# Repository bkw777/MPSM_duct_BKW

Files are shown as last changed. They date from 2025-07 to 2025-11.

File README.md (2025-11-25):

# MPSM_Duct

Hotend fan and part cooling blower duct for Monoprice Select Mini 3d printer.

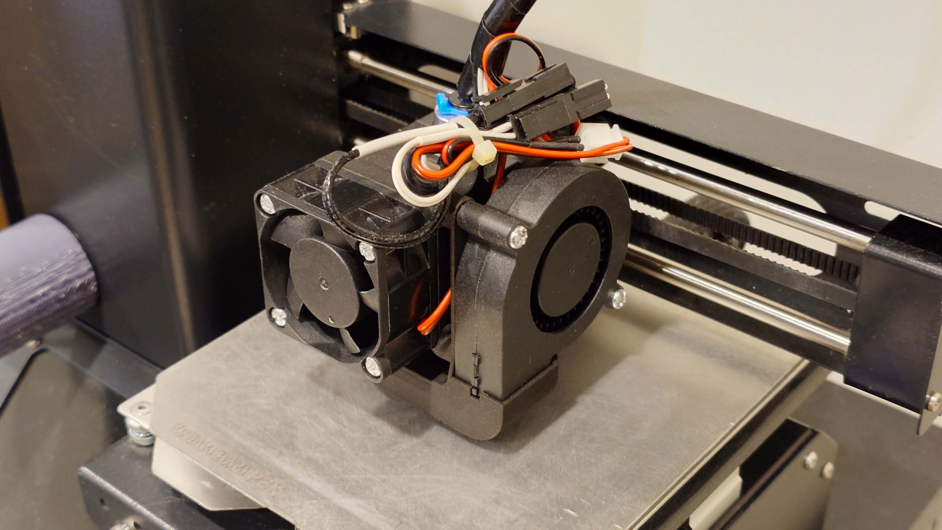
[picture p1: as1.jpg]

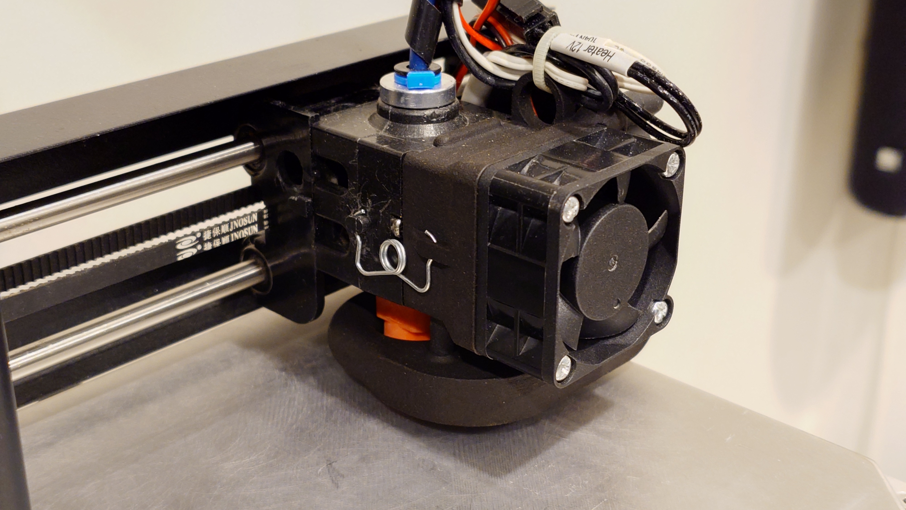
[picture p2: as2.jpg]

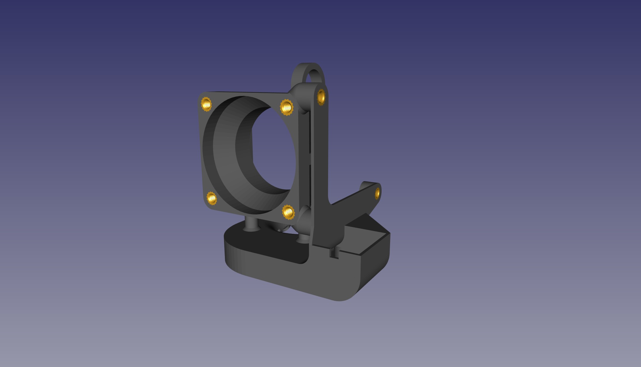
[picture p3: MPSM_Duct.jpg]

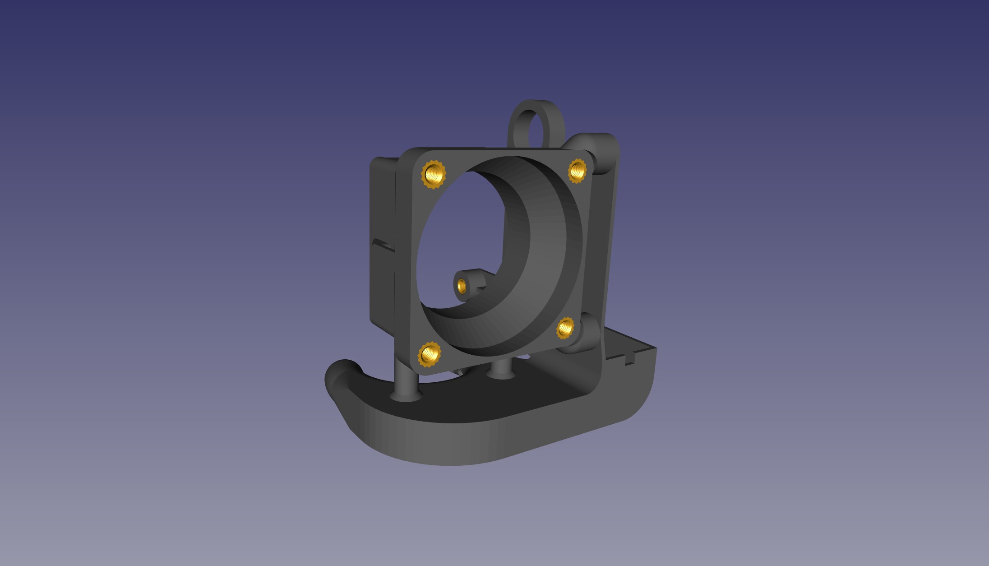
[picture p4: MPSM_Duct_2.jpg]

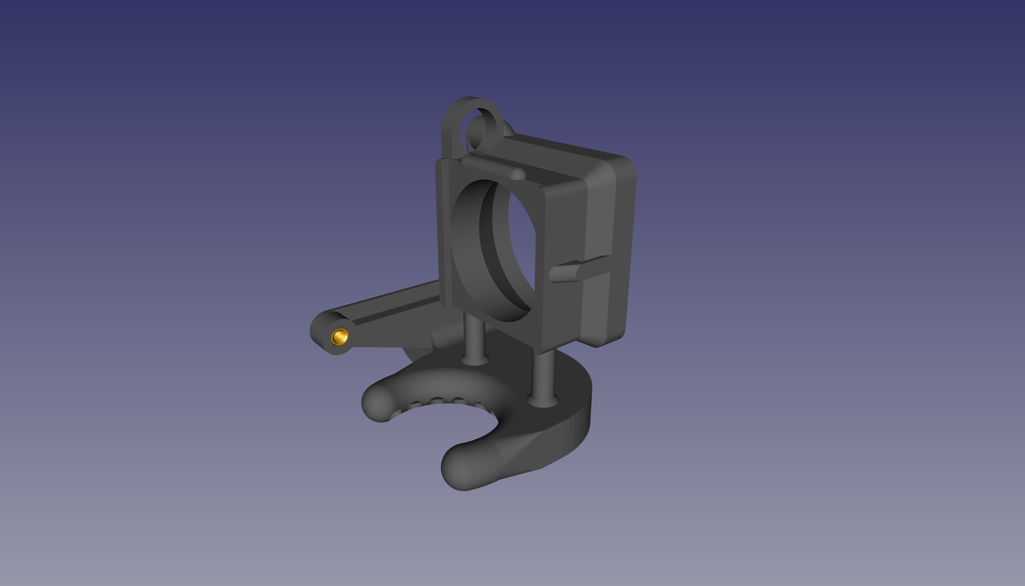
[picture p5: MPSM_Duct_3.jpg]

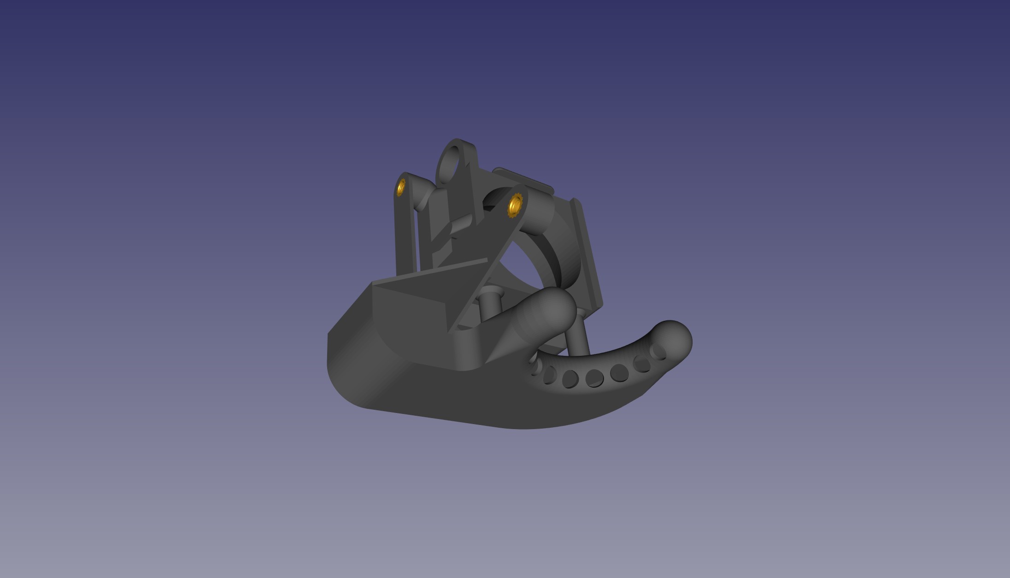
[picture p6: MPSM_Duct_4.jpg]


The model is highly parametric and uses the customizer panel in OpenSCAD to adjust all kinds of things.  

The major options are:  
* Fan size: 40mm, 35mm, 30mm
* Screw holes sized for screwing directly into the plastic, or pockets for heat-set inserts

Other options:
* Stock vs [CHC](https://trianglelab.net/products/chcceramic-heating-core-kit?VariantsId=10256) heater cartridge
* Degrees of wrap around the nozzle.

40mm fan  
You don't need a 40x20 like this. A silent Noctua 40x10 would be plenty considering the original fan is only 30x10 and did both the heat-break and the part cooling.  
By itself a larger fan like this doesn't do as much good as it could, because the stock carriage doesn't provide very much air flow behind the heat-sink. It's intentionally slightly restrictive to force some of the air to go down to the stock part cooling duct. It's possible to drill 4 more holes in the carriage between the heat-sink and the rails without even taking the printer apart. 8mm or 5/16" drill, one vertical in the center right in front of the rails, through the top & bottom, and one horizontal between the rails. Adds 4 more 8-9mm holes for hot-end fan air to exhaust.  
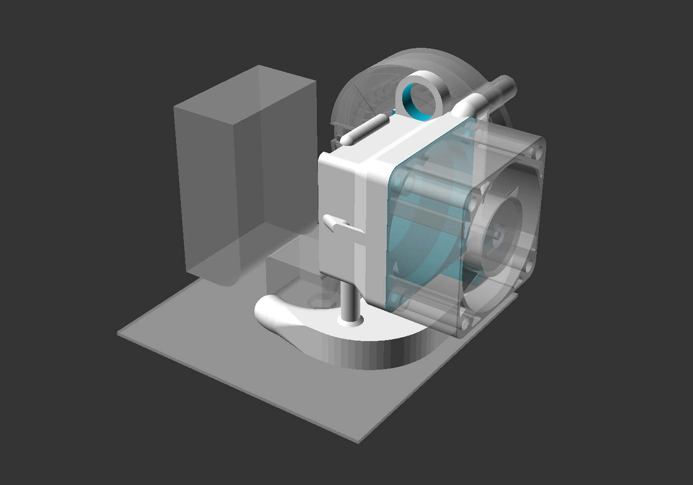
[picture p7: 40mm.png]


35mm fan  
35mm is a less common size but they do exist and the hot-end duct on the printer happens to be 35mm so it looks visually neat.  
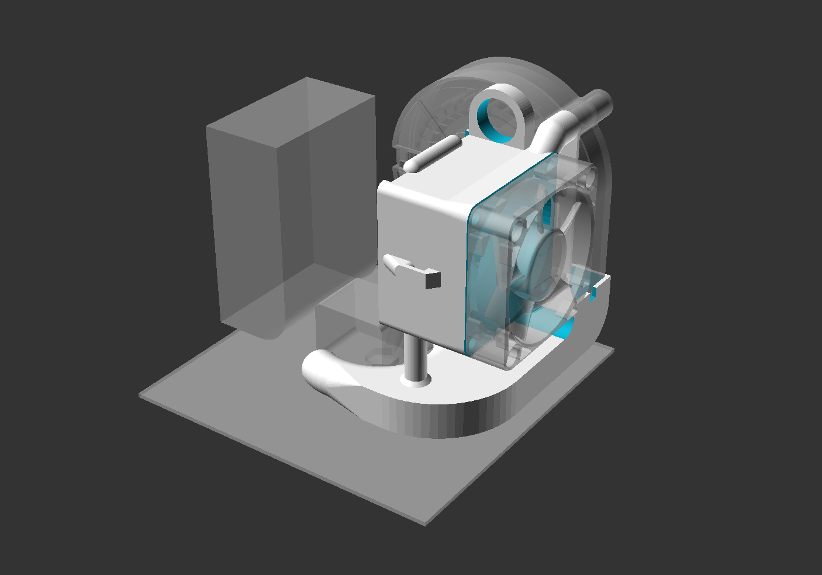
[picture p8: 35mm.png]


30mm fan  
This doesn't look the best, but the usefulness is the original fan is 30mm, so with this version you can re-use the original fan.  
It's still an improvement over stock because now it's dedicated 100% to the heat-break, and remember a standard E3D V6 only has a 30mm fan, so this should actually be fine.  
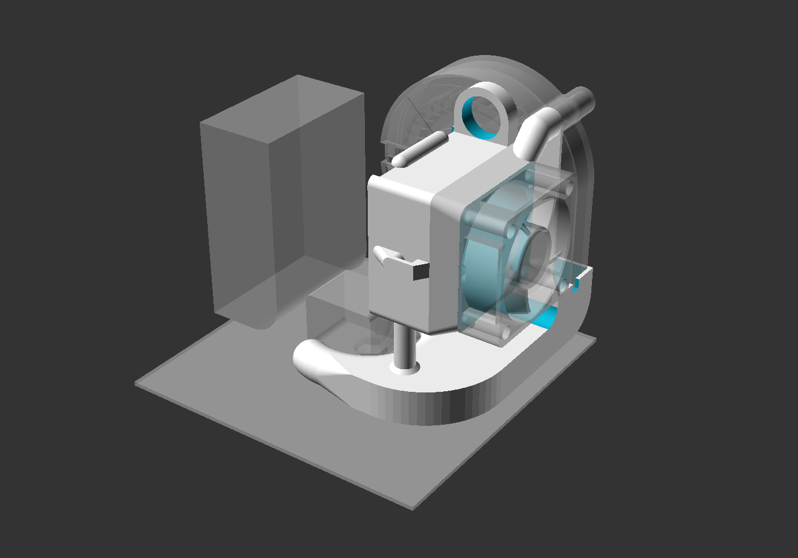
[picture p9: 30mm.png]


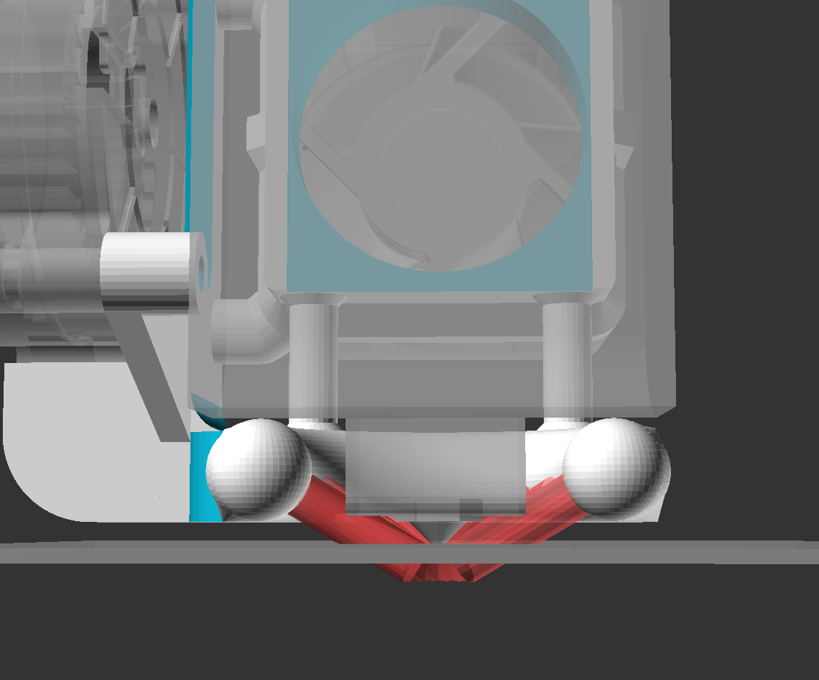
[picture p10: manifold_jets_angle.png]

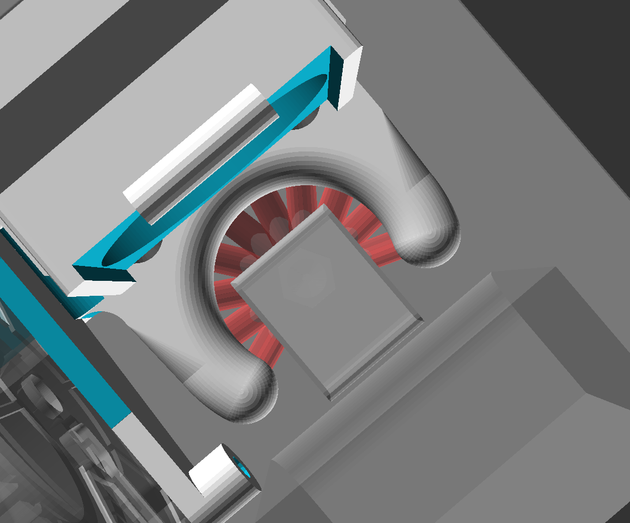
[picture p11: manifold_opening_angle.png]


With a CHC heater, the blower output manifold can go all the way around the nozzle in a donut, and the duct & manifold tube can be a little bigger.

Stock heat block:  
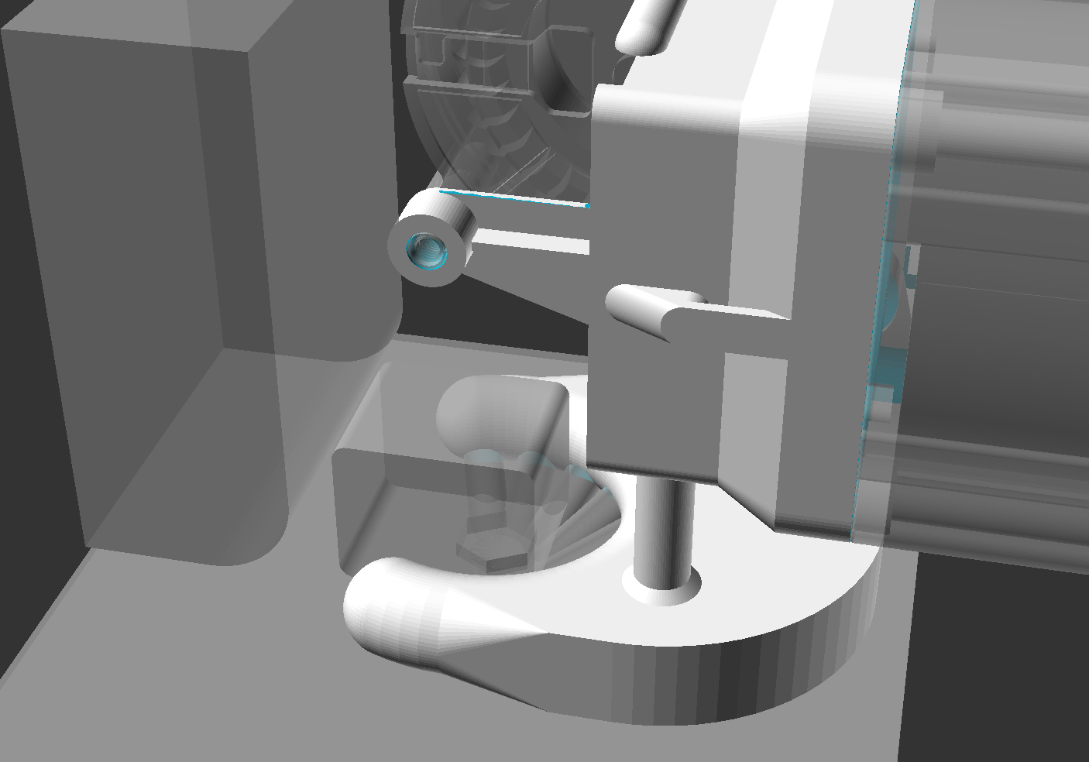
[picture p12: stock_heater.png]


CHC ceramic heater cartridge:  
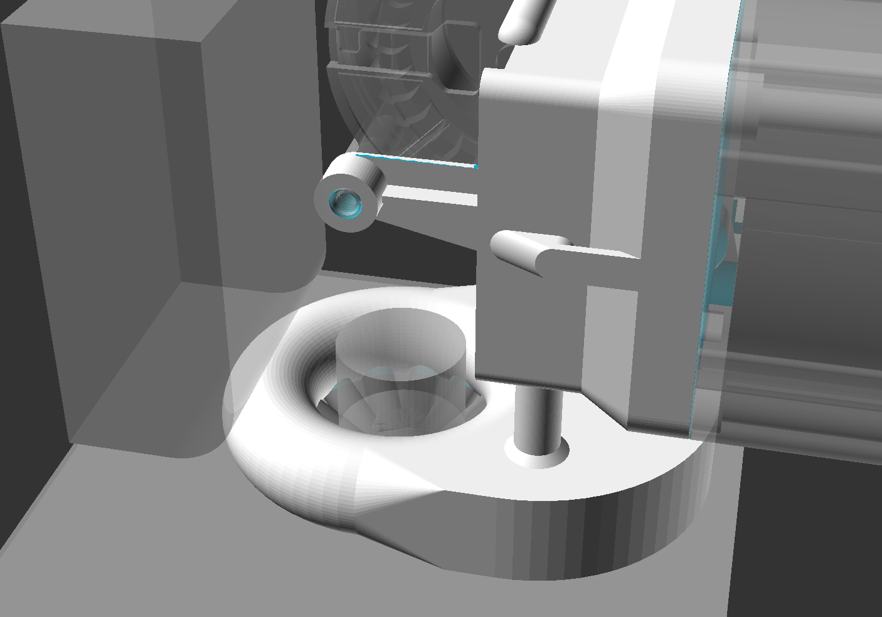
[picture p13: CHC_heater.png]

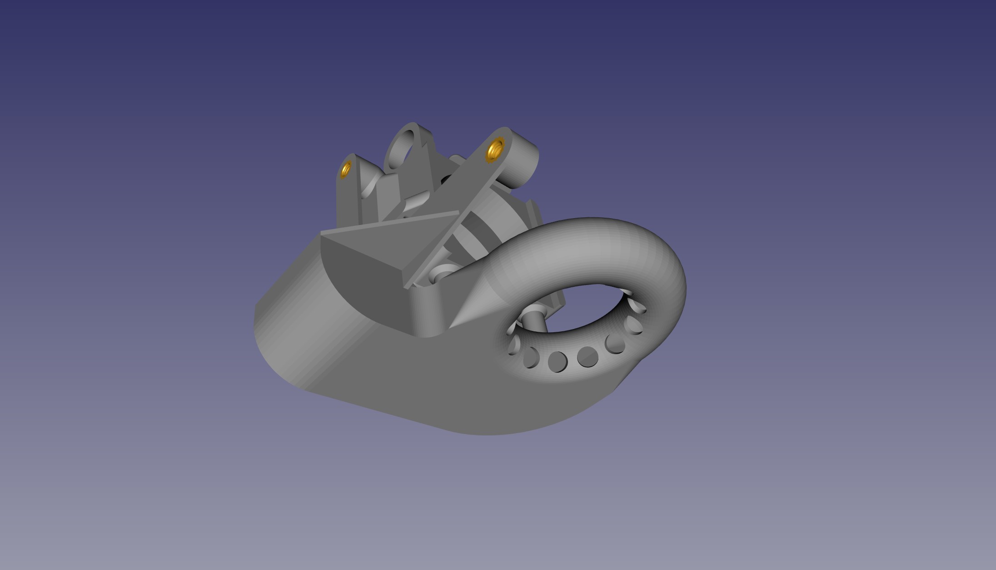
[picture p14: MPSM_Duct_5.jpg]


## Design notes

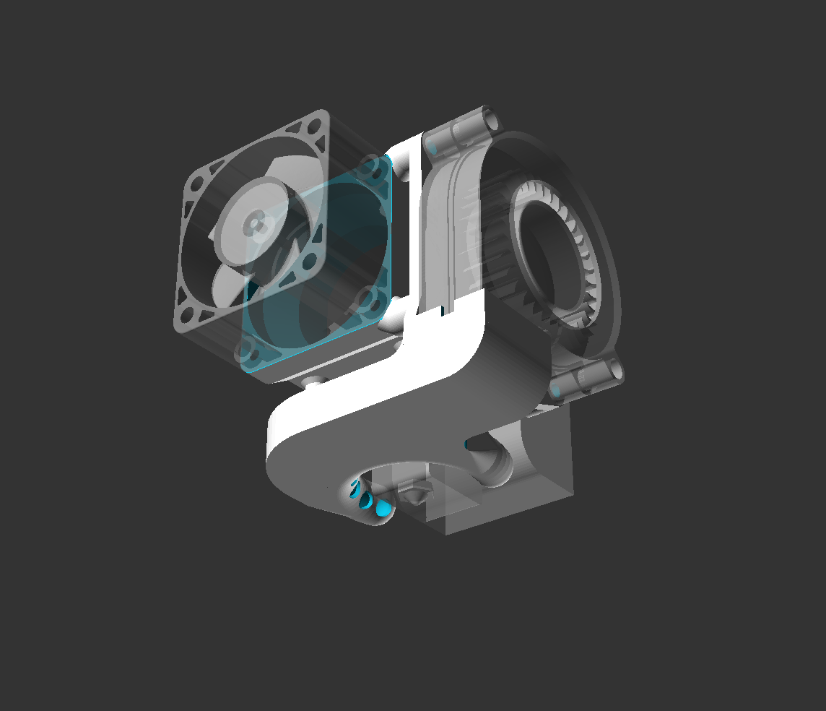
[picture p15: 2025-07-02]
MPSM_Duct_2.png

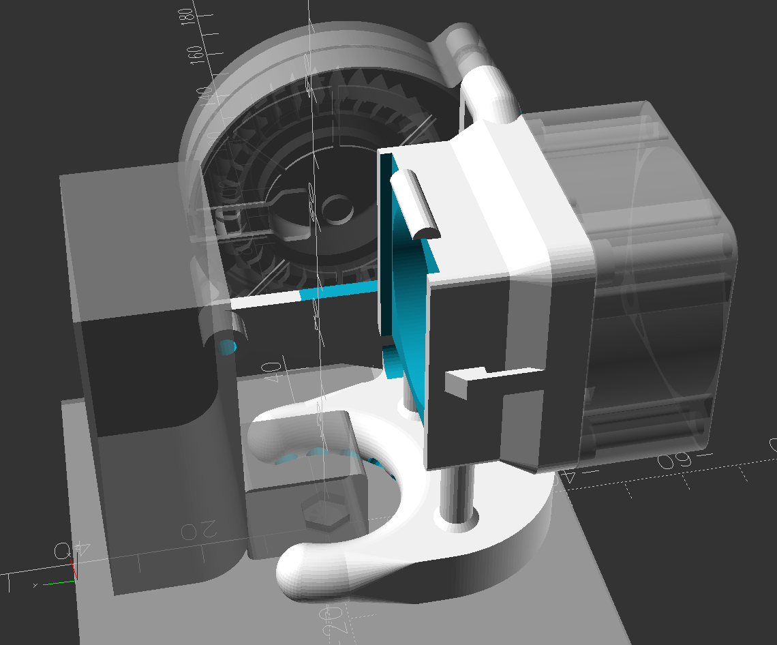
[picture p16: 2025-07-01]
MPSM_Duct_1.png

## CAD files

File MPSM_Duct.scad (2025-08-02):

// Hotend fan and part cooling duct for Monoprice Select Mini V2 E3D
// CC-BY-SA 2025 Brian K. White
//
// Use the Customizer window to select options.
// <design default> = 40mm fan, no screw inserts, stock heat block

hotend_fan_size = 40; // [30,35,40]
hf_w = hotend_fan_size;
screw_hole_inserts = false;
heater_type = "stock"; // ["stock","v6","chc"]


/* [Site Objects] */
show_fans = true;
show_inserts = true;
show_nozzle = true;
show_build_plate = true;
show_carriage = true;
show_jets = true;

/* [Debug Cutaways] */
cutaway_top = false;
cutaway_top_z = 0;
cutaway_bottom = false;
cutaway_bottom_z = 11;
cutaway_left = false;
cutaway_left_x = 0;
cutaway_right = false;
cutaway_right_x = 0;
cutaway_front = false;
cutaway_front_y = -4;
cutaway_back = false;
cutaway_back_y = -4;

/* [Hidden] */
// screw sizes, screw hole id, heatsert hole id, hole depth
// SIZE[ID_bare,ID_heatsert,depth]
M2_5 = [2,3.7,5];
M3 = [2.8,4.3,6];
M4 = [3.6,5.6,8.5];

/* [Misc] */
wire_anchor = true;
clearance_above_print = 2;
fitment_clearance = 0.2;
fc = fitment_clearance;
wall_thickness = 1; // .1
wt = wall_thickness;
small_corner_radius = 2; // .1

top_ledge_style = 2; // [0:"None",1,2,3]

/* [Spring Hooks] */
spring_hook_inset = 6;
hz = spring_hook_inset;
spring_hook_clearance = 3;

/* [Manifold] */
manifold_jets_angle = 35;
manifold_opening_angle = 140;
manifold_jets_diameter = 4; // .1
manifold_jets = 10;

/* [Hotend Fan] */
// hotend fan bolt pattern
hf_bp = 
  (hf_w==30) ? 24 :
  (hf_w==35) ? 29 :
  (hf_w==40) ? 32 :
  (hf_w==50) ? 40 :
  0 ;
//echo("hotend fan size (hf_w)",hf_w);
//echo("hotend fan bolt pattern (hf_bp)",hf_bp);


shd = screw_hole_inserts?1:0;

// -1 = auto
hotend_fan_screw_hole_diameter = -1; // .1
hf_sid =
  (hotend_fan_screw_hole_diameter>=0) ? hotend_fan_screw_hole_diameter :
  (hf_w==30) ? M2_5[shd] :
  (hf_w<=40) ? M3[shd] :
  M4[shd] ;
//echo("hotend fan screw hole id (hf_sid)",hf_sid);

// -1 = auto
hotend_fan_screw_hole_depth = -1; // .1
hf_sih =
  (hotend_fan_screw_hole_depth>=0) ? hotend_fan_screw_hole_depth :
  (hf_w<50) ? 6 : 8 ;
//echo("hotend fan screw hole depth (hf_sih)",hf_sih);

// -1 = auto
hotend_fan_corner_radius = -1; // .1
hf_cr = (hotend_fan_corner_radius<0)?(hf_w-hf_bp)/2:hotend_fan_corner_radius;

hotend_fan_flange_elevation = 14;
hf_fz = hotend_fan_flange_elevation;

// -1 = auto
hotend_fan_flange_thickness = -1;
hf_ft = (hotend_fan_flange_thickness<0)?hf_sih:hotend_fan_flange_thickness;
hf_z = hf_fz + hf_ft;

// hotend fan ID
hf_id = hf_w-wt*2;

hotend_width = 35; // [34:"34 (square, and more room for spring clip)",35:"35 (flush with mating part)"]

/* [Hidden] */
hotend_fan_thickness = 20;
hf_t = hotend_fan_thickness;

// dimensions of various parts, not customizable options

// hotend cover interface
hew = hotend_width;  // hotend width
heh = 34;  // hotend height
// "hotend block" is the step on the hotend cover interface
hebw = 30; // hotend block width
hebt = 2;  // hotend block thickness

// hotend face (z=0) to center of nozzle
nozzle_y = -14;

// center of hotend fan to nozzle tip
nozzle_z = -42;

bottom_y = nozzle_z+clearance_above_print;

total_h = hebt + hf_z;

// part blower
// facing inlet, outlet down
// relative to motor axle
pb_tlx = -23;  // top left screw
pb_tly = 20;   // top left screw
pb_brx = 20;   // bottom right screw
pb_bry = -18;  // bottom right screw
pb_le = -27.5; // left edge
pb_be = -25.5; // bottom edge
pb_ow = 20.1;  // outlet width
pb_od = 15.1;  // outlet depth
pb_oh = 2.5;   // outlet height

/* [Part Blower] */

// -1 = auto
part_blower_screw_hole_diameter = -1; // .1
pb_sid =
  (part_blower_screw_hole_diameter>=0) ? part_blower_screw_hole_diameter :
  M3[shd];
// -1 = auto
part_blower_screw_hole_depth = -1; // .1
pb_sih =
  (part_blower_screw_hole_depth>=0) ? part_blower_screw_hole_depth:
  M3[2];
//echo ("part blower screw hole id,depth (pb_sid,pb_sih)",pb_sid,pb_sih);

part_blower_mount_plate_thickness = 1;
part_blower_lower_post = true;
part_blower_lower_brace_depth = 3;

part_blower_x = 0;
pb_x = part_blower_x + (hf_w>=40 ? hf_w/2+pb_sih : 20+pb_sih);

part_blower_y = -1;
pb_y = part_blower_y;

part_blower_z = 6;
pb_z = part_blower_z;


// manifold width vs height
//
// The Z tower comes to within 21mm from the nozzle,
// so we set a hard limit of 42mm wide for anything
// symmetrical centered on the nozzle.
//
// The size of the manifold tubes is whatever can fit between
// the 42mm max width and the heat block.
/* [Hidden] */
max_manifold_width = 42;

/* [Manifold] */
heater_clearance_radius = 12;
pd_nr = heater_clearance_radius;

// 0 = max
part_cooler_manifold_width = 0;
pd_mw = (part_cooler_manifold_width ? part_cooler_manifold_width : max_manifold_width );
assert(pd_mw<=max_manifold_width,"Manifold width > 42mm hits the Z tower!");
// 0 = auto
part_cooler_manifold_height = 0;
pd_mh = (part_cooler_manifold_height ? part_cooler_manifold_height : pd_mw/2-pd_nr );


// TODO shift 50mm fan off center to avoid hitting Z tower

/* [Part Duct] */
part_cooler_duct_fillet_radius = 4;
pd_fr = part_cooler_duct_fillet_radius;
pillar_diameter = 5;
pillar_chamfer = 1; // .1
pillar_y = -4;

/* [Hidden] */
e = 0.01;
//$fa = 1;
//$fs = $preview?0.6:0.4;
$fn = 72;

module fan () {
  stl =
    hf_w==30 ? "lib/fan3010.stl" :
    hf_w==35 ? "lib/fan3510.stl" :
    hf_w==40 ? "lib/fan4020.stl" :
    "";
  if (stl) import(stl);
}

module blower () {
  import("lib/blower5015.stl");
}

module heatsert (d) {
  echo ("heatsert(d)",d);
  if ( (d>M2_5[1]-0.5) && (d<M2_5[1]+0.5) ) rotate([180,0,0]) import("lib/insert_m2_5.stl");
  else if ( (d>M3[1]-0.5) && (d<M3[1]+0.5) ) rotate([180,0,0]) import("lib/insert_m3.stl");
  else if ( (d>M4[1]-0.5) && (d<M4[1]+0.5) ) rotate([180,0,0]) import("lib/insert_m4.stl");
}

module mirror_copy(v = [1, 0, 0]) {
  children();
  if (v[0]||v[1]||v[2]) mirror(v) children();
}

module qc (w=10,d=10,h=10,r=1) {
  mirror_copy([0,1,0]) translate([0,d/2,0])
    mirror_copy([1,0,0]) translate([w/2,0,0])
      cylinder(h=h,r=(r<e?e:r));
}

module sqylinder(w=10,d=10,h=10,r=1) {
  if (r<=0) translate([-w/2,-d/2,0]) cube([w,d,h]);
  else hull() qc(w=w-r*2,d=d-r*2,h=h,r=r);
}

module fan_flange (w,s,h,r,d,t=wt) {
  ch = h+2*e;
  id = w-2*t;
  difference() {
    sqylinder(w=w,d=w,h=h,r=r);
    translate([0,0,-e]) {
      qc(w=s,d=s,h=ch,r=d/2);
      cylinder(d=id,h=ch);
    }
  }
}

module taurus(R=10,r=4,A=360,a=0){
  rotate_extrude(angle=A,start=a) translate([R-r,0,0]) circle(r=r);
}

module nozzle () {
  //nozzle
  pd = 1.25; // point diameter
  ph = 2;    // point height
  hh = (heater_type=="stock"?2:3);    // hex height
  cylinder(d1=pd,d2=pd+2*ph,h=ph);
  translate([0,0,ph]) cylinder(d=8.1,h=hh,$fn=6);

  // heat block
  if (heater_type=="v6") {
    w = 16;
    d = 23;
    h = 12;
    s = 1.5; // sock thickness
    i = 8; // inset, nozzle to edge
    translate([0,d/2-8,h/2+ph+hh])
      cube([w+2*s,d+2*s,h+2*s],center=true);
  } else if (heater_type=="chc") {
    translate([0,0,ph+hh])
      cylinder(d=15,h=12);
  } else {
    // stock
    w = 15;
    d = 16;
    h = 12;
    b = 1.5; // blanket thickness
    i = 4; // inset (nozzle to edge)
    translate([w/2,d/2-i,h/2+ph+hh])
      rotate([-90,0,90])
        sqylinder(w=d+2*b,d=h+2*b,h=w,r=b);
  }

}

module carriage () {
  w = 35;
  d = 20;
  h = 50;
  y = 14; // nozzle to front of carriage
  z = 10; // nozzle to bottom of carriage
  r = 8;
  hull() {
    translate([-w/2,y+d-e,z]) cube([w,e,e]);
    translate([-w/2,y+d-e,z+h-e]) cube([w,e,e]);
    translate([-w/2,y,z+h-e]) cube([w,e,e]);
    translate([-w/2,r+y,r+z]) rotate([0,90,0]) cylinder(r=r,h=w);
  }
}


//////////////////////////////////////////////////////////////////////////////////

module anchor() {
  w = hf_fz;
  d = w/2;
  h = 4;
  difference() {
    group() {
      translate([0,d,0]) cylinder(d=w,h=h);
      translate([-w/2,0,0]) cube([w,d,h]);
    }
    translate([0,d,-e]) cylinder(d=w-4,h=h+2*e);
  }
}

module hotend_fan_duct() {
  if(show_fans) translate([0,0,hf_z]) %fan();
  if(screw_hole_inserts && show_inserts)
    mirror_copy([0,1,0]) mirror_copy([1,0,0]) translate([hf_bp/2,hf_bp/2,hf_z]) %heatsert(hf_sid);
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

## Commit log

2025-06-30 polish blower mount
    [MPSM_duct_BKW.scad]
2025-07-01 fillets on duct, hotend models
    [MPSM_duct_BKW.scad]
2025-07-01 clean a few seams, toggle air jets view
    [MPSM_duct_BKW.scad]
2025-07-02 fix thin wall, seams in manifold, debug cutaways
    [MPSM_duct_BKW.scad]
2025-07-02 missing lib/ stls, notch in blower-duct interface
    [MPSM_duct_BKW.scad]
2025-07-03 special comments for decimal values in customizer
    [MPSM_duct_BKW.scad]
2025-07-04 seams & wall thickness on duct fillets, gusset on blower mount
    [MPSM_duct_BKW.scad]
2025-07-08 blower mount: thin plate w/rib, m3 screws
    [MPSM_duct_BKW.scad]
2025-07-08 wire anchor
    [MPSM_duct_BKW.scad]
2025-07-19 reduce screw insert bore id, rounded clip hook
    [MPSM_duct_BKW.scad]
2025-08-02 tighter fit to gantry
    [MPSM_duct_BKW.scad]
